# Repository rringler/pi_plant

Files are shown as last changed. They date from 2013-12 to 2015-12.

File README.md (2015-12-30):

# pi_plant

pi_plant screenshot

## Overview
(Long) weekend project to monitor and water my plant with a Raspberry Pi.  The
app was developed for Raspbian Wheezy with an
[arduino two-prong soil moisture sensor](http://www.amazon.com/s/ref=nb_sb_noss?url=search-alias%3Daps&field-keywords=arduino%20soil%20sensor)
via a MCP3002 analog-to-digital converter, and an
[arduino relay board](http://www.amazon.com/s/ref=nb_sb_noss?url=search-alias%3Daps&field-keywords=arduino%20relay%20board)
to control a 110 VAC water pump.

It makes a couple of assumptions:

### Moisture Sensor:
* Now includes a [Kicad](http://kicad-pcb.org/) PCB design for interfacing with
a MCP3002 10-bit SPI Analog-to-Digital Converter. The Pi talks to the ADC via
its SPI interface.  Includes all the manufacturing files required to fab the
board (which I had [OSH Park](https://oshpark.com/) make for me for $7.85
shipped, which required about $15 in components from
[Digi-key](http://www.digikey.com/).)

  Custom PCB Layout

* Includes three 2N3904 transistors to allow the Pi to control the power
provided to the MCP3002 & the two analog sensors:

  NPN-Transistor Network

(Leaving these two-prong type of sensors powered on 24/7 can lead to galvanic
corrosion, so it's probably better to turn them on when needed.)

* Provides two analog measurement channels.  Also supplies VCC & GND (in case
the moisture sensor requires it) for each.

### Water Pump:
* Assumes there is a power pin to activate the pump.  My Pi's 3.3V GPIO was able
to activate/deactivate my relay board directly, but if you're having issues you
could always use a NPN-transistor network as shown above.

## Dependencies
pi_plant was developed on Ruby v2.1 and Rails v4.0.  Several gems were utilized
to make development easier:

```ruby
gem 'bootstrap-sass', github: 'thomas-mcdonald/bootstrap-sass'
gem 'figaro'
gem 'draper'
gem 'lazy_high_charts'
```

## Installation
1. Clone the repository.
2. Create a `/config/application.yml` file with environmental variables holding
all your secret keys (see [figaro's](https://github.com/laserlemon/figaro)
documentation for more details) and add it to your `.gitignore` file.

   ```ruby
   RAILS_SECRET_KEY_BASE: '<rails secret key>'
   ```

3. Schedule the `sample` rake task to take periodic soil measurements.

   ```ruby
   crontab -e
   00 00, 12, * * * * rvmsudo rake RAILS_ENV=production sample
   ```
   Note: the Pi requires root access to interact with hardware

4. Start the webserver
5. Create a plant with the GPIO pins used in your circuit.

## Bill of Materials
| Find No. | Qty | Part Number | Description | Approx. Extended Cost |
|---:|----:|:---|:---|---:|
| 1 | 1 | 756-8308 | [Raspberry Pi v2](https://www.adafruit.com/products/2358) | $40 |
| 2 | 1 | SDC10/8GBET | [Kingston 8GB microSD Card](http://www.amazon.com/gp/product/B008EODGHS) | $8 |
| 3 | 1 | EW-7811Un | [Edimax 802.11n USB Adapter](http://www.amazon.com/gp/product/B003MTTJOY) | $10 |
| 4 | 1 | B00E0NTPP4 | [SunFounder 2 Channel 5V Relay Shield for Arduino](http://www.amazon.com/SunFounder-Channel-Shield-Arduino-Raspberry/dp/B00E0NTPP4/) | $7 |
| 5 | 1 | B00AYCNEKW | [sunkee Soil Moisture Sensor](http://www.amazon.com/gp/product/B00AYCNEKW) | $3 |
| 6 | 1 | B001BOD9JI | [TOM 3.5gph Aquarium Pump](http://www.amazon.com/gp/product/B001BOD9JI) | $16 |
| 7 | 1 | kTJJCOss | [OSH Park Custom PCB](https://oshpark.com/shared_projects/kTJJCOss) | $8 |
| 8 | 1 | MCP3002-I/P | [MCP3002 2-Channel 10-bit ADC](http://www.digikey.com/scripts/DkSearch/dksus.dll?Detail&itemSeq=186693142&uq=635870217430541403) | $2 |
| 9 | 3 | 2N3904BU | [40V NPN Transistor](http://www.digikey.com/scripts/DkSearch/dksus.dll?Detail&itemSeq=186700114&uq=635870217430551404) | $1 |
| 10 | 3 | CF14JT1K00 | [1kOhm 1/4W Carbon Through Hole Resistor](http://www.digikey.com/scripts/DkSearch/dksus.dll?Detail&itemSeq=186693725&uq=635870217430551404) | $1 |
| 11 | 2 | 0022288363 | [Molex 36pos Right-Angle Pin Header](http://www.digikey.com/scripts/DkSearch/dksus.dll?Detail&itemSeq=186693603&uq=635870217430541403) | $4 |

## TODO
 - [X] Custom PCB for interfacing with the MCP3002 (experimenting with Kicad)

## Keywords
 - Raspberry Pi
 - RPi
 - Ruby on Rails
 - Kicad
 - MCP3002
 - Home Automation

## Credits
pi_plant is the product of [Ryan Ringler](http://github.com/rringler).  It was
developed as a (long) weekend project to experiment with the Raspberry Pi,
Rails, and Kicad.

## License
pi_plant is licensed under the MIT License.  Please see the
[LICENSE](http://github.com/rringler/pi_plant/LICENSE) file for additional
details.

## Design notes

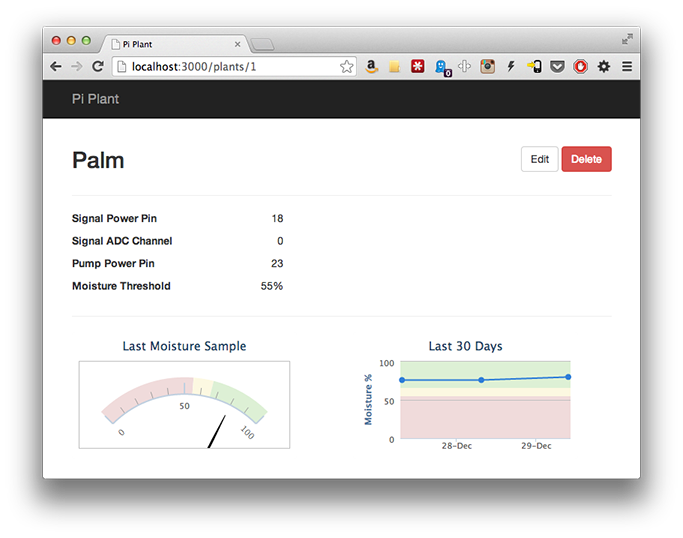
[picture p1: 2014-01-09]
public/images/screenshot.png

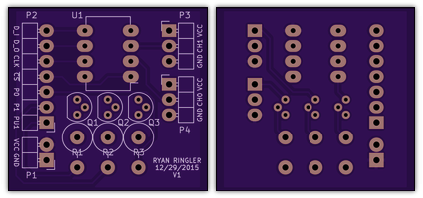
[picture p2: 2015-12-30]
public/images/mcp3002_v1.png

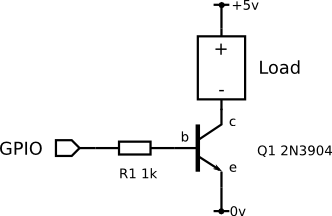
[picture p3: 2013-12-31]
public/images/npn_switch.png

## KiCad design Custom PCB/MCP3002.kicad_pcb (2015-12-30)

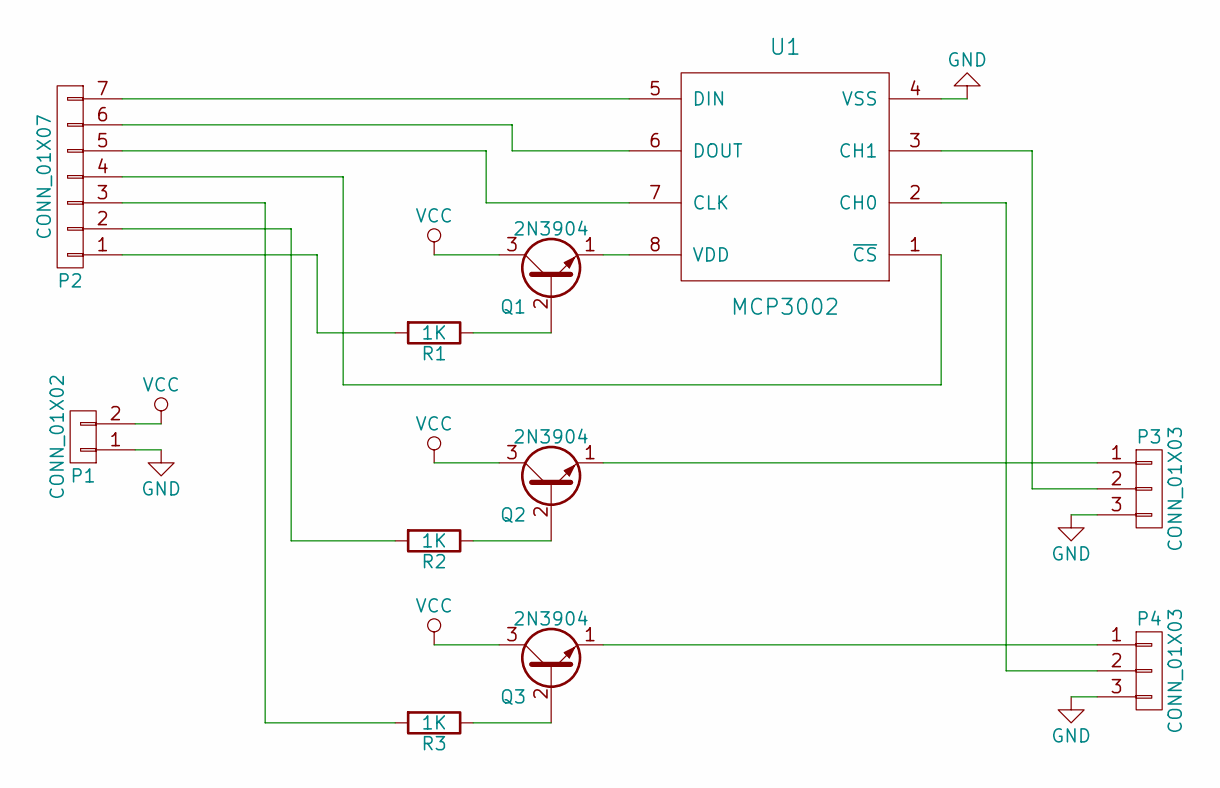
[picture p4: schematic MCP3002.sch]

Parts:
P1: CONN_01X02; Pin_Header_Angled_1x02_No_Pins
P2: CONN_01X07; Pin_Header_Angled_1x07_No_Pins
P3, P4: CONN_01X03; Pin_Header_Angled_1x03_No_Pins
Q1, Q2, Q3: 2N3904; TO-92_Molded_Narrow
R1, R2, R3: 1K; Resistor_Vertical_RM5mm
U1: MCP3002; DIP-8_W7.62mm_LongPads

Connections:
GND: P1.1, P3.3, P4.3, U1.4 (VSS)
unnamed: P2.1, R1.2
unnamed: P2.2, R2.2
unnamed: P2.3, R3.2
unnamed: P2.4, U1.1 (~CS)
unnamed: P2.5, U1.7 (CLK)
unnamed: P2.6, U1.6 (DOUT)
unnamed: P2.7, U1.5 (DIN)
unnamed: P3.1, Q2.1 (E)
unnamed: P3.2, U1.3 (CH1)
unnamed: P4.1, Q3.1 (E)
unnamed: P4.2, U1.2 (CH0)
unnamed: Q1.1 (E), U1.8 (VDD)
unnamed: Q1.2 (B), R1.1
unnamed: Q2.2 (B), R2.1
unnamed: Q3.2 (B), R3.1
VCC: P1.2, Q1.3 (C), Q2.3 (C), Q3.3 (C)

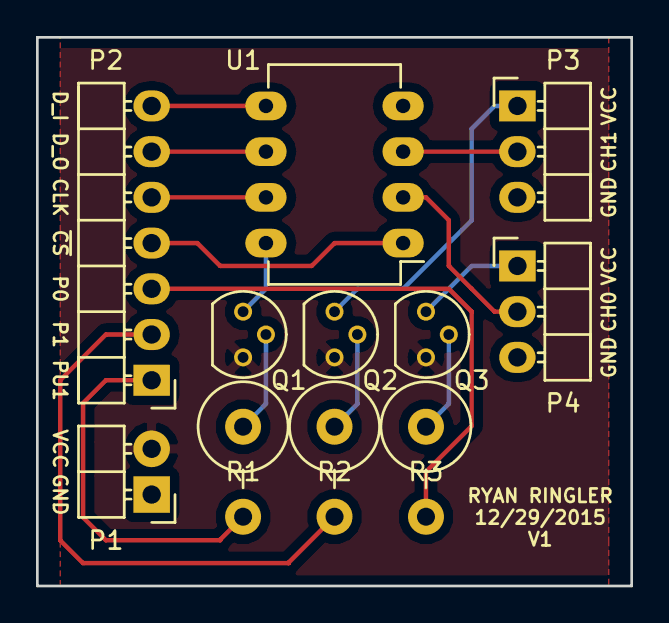
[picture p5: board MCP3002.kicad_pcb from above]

Board: 2 copper layers, 33.0 x 30.5 mm, 11 parts (0 on the bottom side), 17 nets.

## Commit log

2013-12-27 Creates a new rails app with plant and sample models.
2013-12-29 Creates pump and sensor models to handle RPi GPIO & SPI operations.
2013-12-29 Creates factories for plant and sample models.
2013-12-29 Updates migrations to make moisture samples integers, and adds a moisture_threshold to all plants.
2013-12-29 Improves rake task to perform sensor sampling and pump watering logic.
2013-12-29 Adds recent(n) and most_recent scopes to the Sample model, so smaller datasets can be plotted.
2014-01-03 Updates pi_plant gem to use a fork until SPI fixes are merged into master.
2014-01-05 Updates pi_plant gem to use the original. Pull Requests #15 & #17 fixing SPI communication have been merged.
2014-01-05 Improves pump & sensor error checking to limit valid pins to just the valid GPIO pins.
2014-01-05 Improves error checking for plant, pump, and sensor models.
2014-01-05 Updates the pi_plant:sample rake task to use the new method names.
2014-01-09 Updates plant sensor creation method with measured min/max options.
2014-01-09 Inverts sensor#percentile method so that 100% is max moisture and 0% is min moisture.
2014-01-09 Improves styling on the plant edit & delete buttons.
2014-01-12 Improves link_to call to remove Rails 4.1 deprecation warning.
2015-12-30 Adds Kicad PCB Layout for MCP3002 A/D Converter
    Adds Kicad PCB layout for the MCP3002 A/D converter used in the design.
    [MCP3002-B.Cu.gbl, MCP3002-B.Mask.gbs, MCP3002-B.SilkS.gbo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]
2015-12-30 Updates the README to reference the MCP3002
    Updates the README to reference the MCP3002, and the new PCB layout.
2015-12-30 Adds Bill of Materials to README
    Adds a Bill of Materials to the README.
